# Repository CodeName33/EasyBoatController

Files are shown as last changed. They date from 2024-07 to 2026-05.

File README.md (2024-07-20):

# About

This is simple boat/yacht autopilot application (outboard motor only, not for sails). It uses android phone as main device and special diy hardware to move boat rudder.

# How to build hardware device

You need to buy some parts and print plastic parts with 3D Printer.

What to buy:
 - ESP32 Wroom

 - Nema 17 Stepper motor (17HS4401) (With cable)
 - Driver A4988

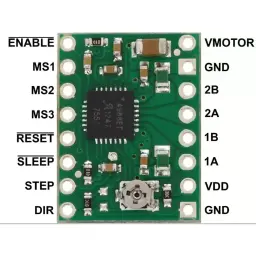
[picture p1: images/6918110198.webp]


 - Extension board for A4988

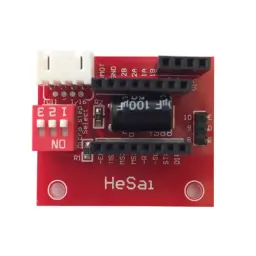
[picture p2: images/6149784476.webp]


 - Flange support bearing KFL08 8mm (2pc)

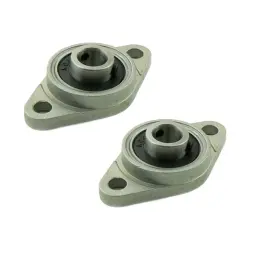
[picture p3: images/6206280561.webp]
 
 
 - Linear bearing LM8UU (2pc)
 - Round guide 8mm 500mm (2pc)

 - Rigid coupling 5x8

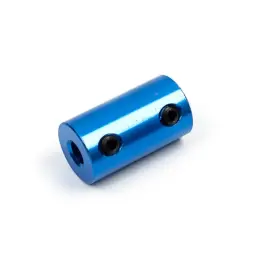
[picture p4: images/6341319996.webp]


 - Nut for screw TR8 pitch 2mm, stroke 8mm

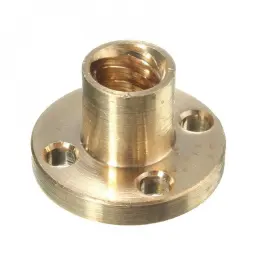
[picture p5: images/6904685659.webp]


 - Trapezoidal screw TR8x8 500mm

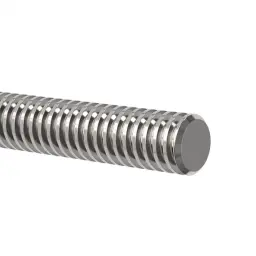
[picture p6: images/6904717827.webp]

 - 12v to 5v buck module (Any)
 - 12v accumulator
 - Bolts M3x10mm-12mm (4pcs), M3x16mm (4pcs)
 - Bolts M4x15mm (12pcs)
 - Bolts M5x30mm (2pcs), M5x25mm (1pc), M5x50mm (6pcs), M5x10mm (2pcs), M5x60mm (1pc)
 - Nuts M4 (12pcs)
 - Nuts M5 (12pcs)

Print all parts from Hardware/all-parts file. There are OpenSCAD source too, so you can change any parameters.

Hardware/how-to-assemble.3mf shows how to build. Black parts must be printed using hard plastic (I've used PETG carbon fibre) white parts can be printed using TPU.

Install A4988 to Extension board. Connect Nema 17 to Extension board.

Soldering:

E (Extension board) = GPIO4 (ESP32)

D (Extension board) = GPIO16 (ESP32)

S (Extension board) = GPIO17 (ESP32)

GND (Extension board, any GND) = GND (ESP32)

5v (Extension board) = 3v3 (ESP32)

9v (Extension board) = 12v+ (Power input)

12v+ (Power input) = IN+ (12v to 5v buck module)

12v- (Power input) = IN- (12v to 5v buck module)

OUT+ (12v to 5v buck module) = 5v (ESP32)

OUT- (12v to 5v buck module) = GND (ESP32)

Assembled device:
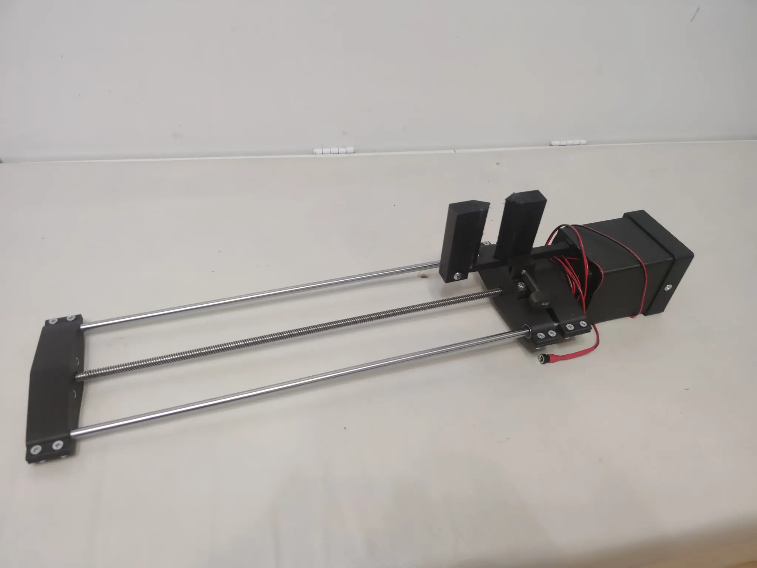
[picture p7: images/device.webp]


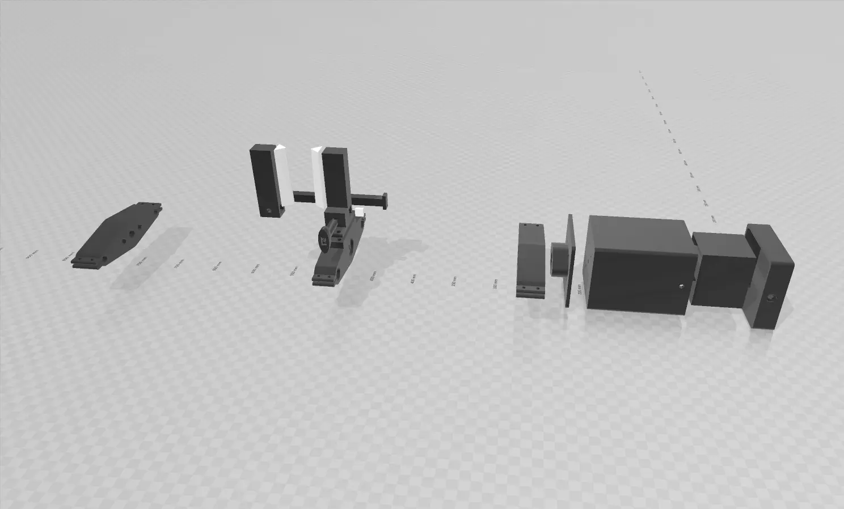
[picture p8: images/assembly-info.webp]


Use 2 fusion nut in holes at bottom of device (yes there are bottom and holes at bottom side). I've used 1/4 nut like in cameras and can use magic arms to hold device on boat.

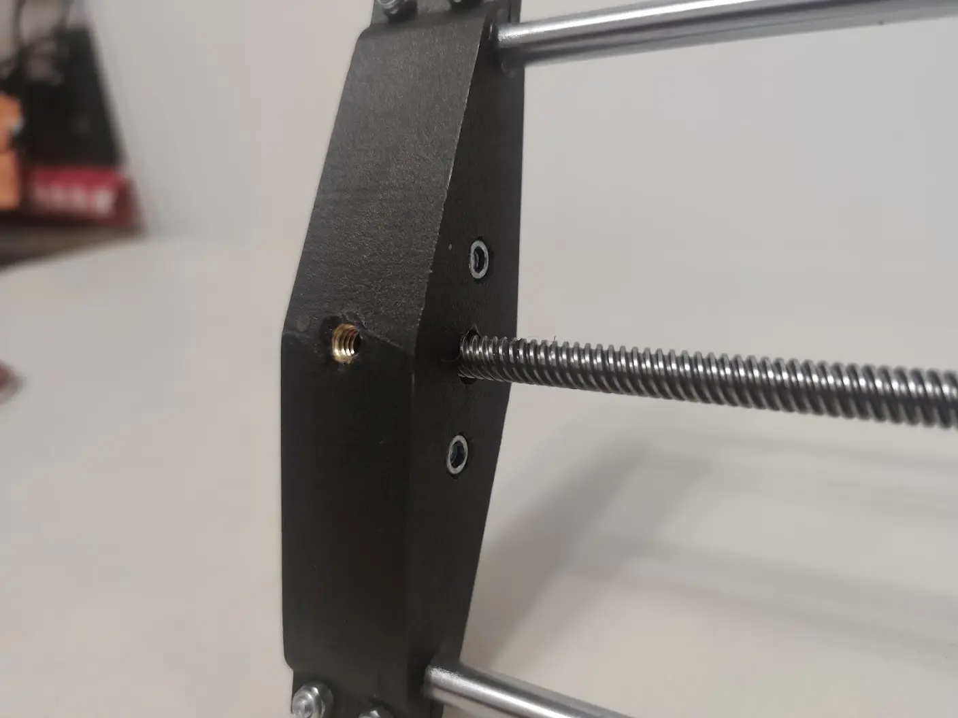
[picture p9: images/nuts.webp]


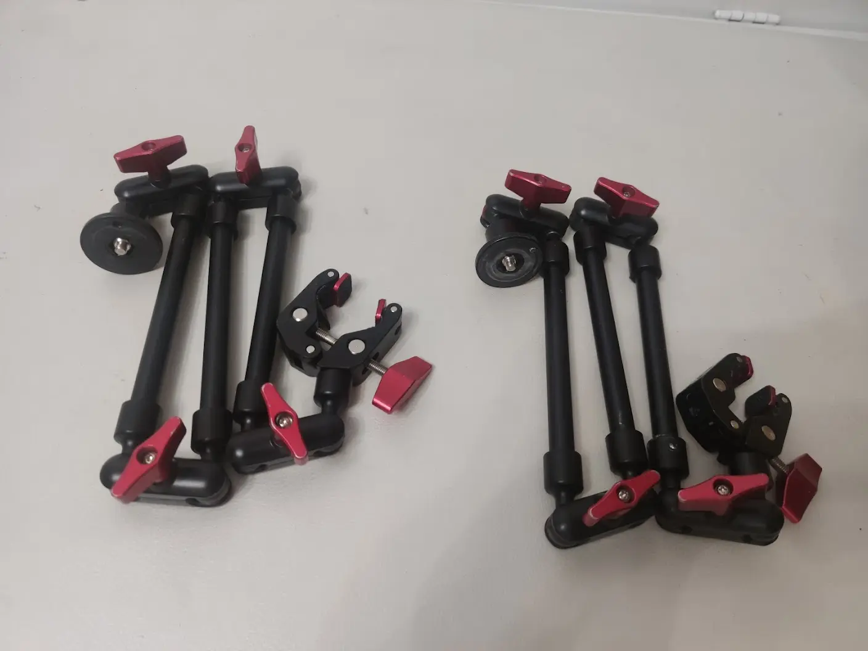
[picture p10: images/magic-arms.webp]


# Using Software

There are two ways:

1. Your own hosting for web-app (put manifest.json, index.htm and icon.png to your host)
2. Use my web-site (http://codename33.ru/apps/ebc/)

Using chrome on your mobile device on notebook goto http://codename33.ru/apps/ebc/ (or your own url).

Install EasyBoatController as desktop application. Now you have app installed (it will work even without internet after first run).

# Using Both parts

Power on hardware part (it has no buttons and indicators, just need to supply 12v power)

Press "Connect Bluetooth" button in EasyBoatController application. If all soldered right and worked you can see device named "EasyBoatController", connect to it.

Press "Calibrate" button and press "Run auto zero calibration" button. This will move caret to end and after some time to middle. 

Set the steering tiller level to zero and put tiller steering into tiller steering lock and lock it.

Now you can hold hardware device on boat. If you are using magic arms - fix device in current position.

You can test device using "Start Accel Drive" button. It will move the rudder when you when you tilt your phone (like in phone games).

For now this allication can't show maps but it can import route in KML or GPX format. You can make your own route in Navionics Boating or  this service for example (https://www.gpsvisualizer.com/draw/) and export GPX file.

In EasyBoatController application press "Route Management..." and next press "Import..." and open your GPX or KML file. You can save/load this route in application now.

Now you can start your engine wit preferred speed and press button "Start Navigation". 

**IMPORTANT NOTE**: You can't turn your screen off or switch to another application while navigating, web-apps can't work in background on android (Yes, ServiceWorkers, but no BLE for them). May be you want to rewrite my js code and make apk that can work in background, I don't want it now ;) I made special button called "Black Screen" it fills screen in black with some gray text on it. This can save battery for devices with OLED displays.

# Application Settings Description

**Course** - settings for navigation
 - **Maximum Rudder Position Percent** - zone in which rudder can move (100% - full)
 - **Keep Boat Near Lines** - In navigation mode this chack will force autopilot to move boat near lines between course points
 - **Taking Points Not Necessary** - If checked this means that boat don't need to move near points, to got it. It unchecked "Points - Distance To Point To Be Done" option works
 - **Keep Boat Near Line Q** - This value makes alutopilot try to move boat to line faster. Too high value can make boat make zigzags over line. 1.5 - 3.0 recommended.
 - **Keep Boat Near Line Max Percent** - very similar to "Keep Boat Near Line Q" option but in percents

 - **Points** - points options
     - **Distance To Point To Be Done** - works only when "Taking Points Not Necessary" unckecked. Distance in meters.

 - **Speed Compensation For Slow Rudder** - this algorythm use boat speed to limit rudder move zone (like "Maximum Rudder Position Percent" option). On high speed boat with slow rudder move speed it can help to navigate better.
     - **Enabled** - turns on or off this algorythm
     - **Compensate After Speed Kmh** - compensation will start after this speed (in km/h).
     - **Compensate Min Q** - minimum rudder zone (0.1 = 10% etc)
     - **Angle To Point Dont Compensate After** - Turn off compensation when difference between boat angle and cource angle more then this value,
**Gps** - GPS  options
 - **Use Compass Between Gps Steps** - it can increase cource accuracy, but you don't need to move youyr phone while navigating.
 - **Meters To Move** - GPS position must be changed to value more then in this option to calculate boat course. This option can help avoid course jumping cause of gps random inaccuracy (removed by default (0) in last version)
 - **Points To Group** - Algorythm takes averages GPS coordinates from count of this points. Also can help avoid course jumping cause of gps random inaccuracy
 
**Calibrate** - calibration options
 - **Max Steps** - max steps (from left to right position). If you use 500mm trapezoidal screw and round guides leave default
 - **Auto Calibration Center** - steps from side to center. If you use 500mm trapezoidal screw and round guides leave default
 - **Default Side Max** - default values for side to center that will be set after "Run auto zero calibration" button
 - **Inverted Move** - inversion for rudder

**Emulation** - emulation options
 - **Enabled** - turn on/off emulation mode
 - **Wind** - Wind in emulation
     - **Angle** - wind angle
     - **Force** - wind force. 0 - off, value - wind speed, but not in km/h in GPS distances (something like 0.00001)
 - **Offsets**
     - **Rudder Rotate** - static boat rotation (0 - off)
 - **Boat** - Boat options
     - **Speed** - boat speed,but not in km/h in GPS distances (something like 0.00002)
     - **Rudder Speed** - speed of rudder movements
     - **Delay Seconds** - delay for coordinates (GPS emulation) in seconds

**AccelDrive** - Accelerometer Drive Options
 - **Min Angle To Move** - minimum angle changes to accept. This can avoid many garbage changes.
 
# Some Videos

## EasyBoatController - Steering Wheel Test
IMAGE ALT TEXT (http://www.youtube.com/watch?v=HxvT-cGLmB0 "EasyBoatController - Steering Wheel Test")

## EasyBoatController - Rudder Lock Testing
IMAGE ALT TEXT (http://www.youtube.com/watch?v=xiY143fznu8 "EasyBoatController - Rudder Lock Testing")

## EasyBoatController - Movements Test
IMAGE ALT TEXT (http://www.youtube.com/watch?v=BEtO-wEw2SI "EasyBoatController - Movements Test")

## EasyBoatController - Short Creating And Testing
IMAGE ALT TEXT (http://www.youtube.com/watch?v=R22tecXQIwo "EasyBoatController - Short Creating And Testing")

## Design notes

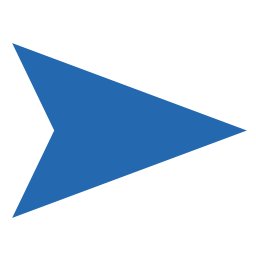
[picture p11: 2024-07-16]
Software/Web/boat.png

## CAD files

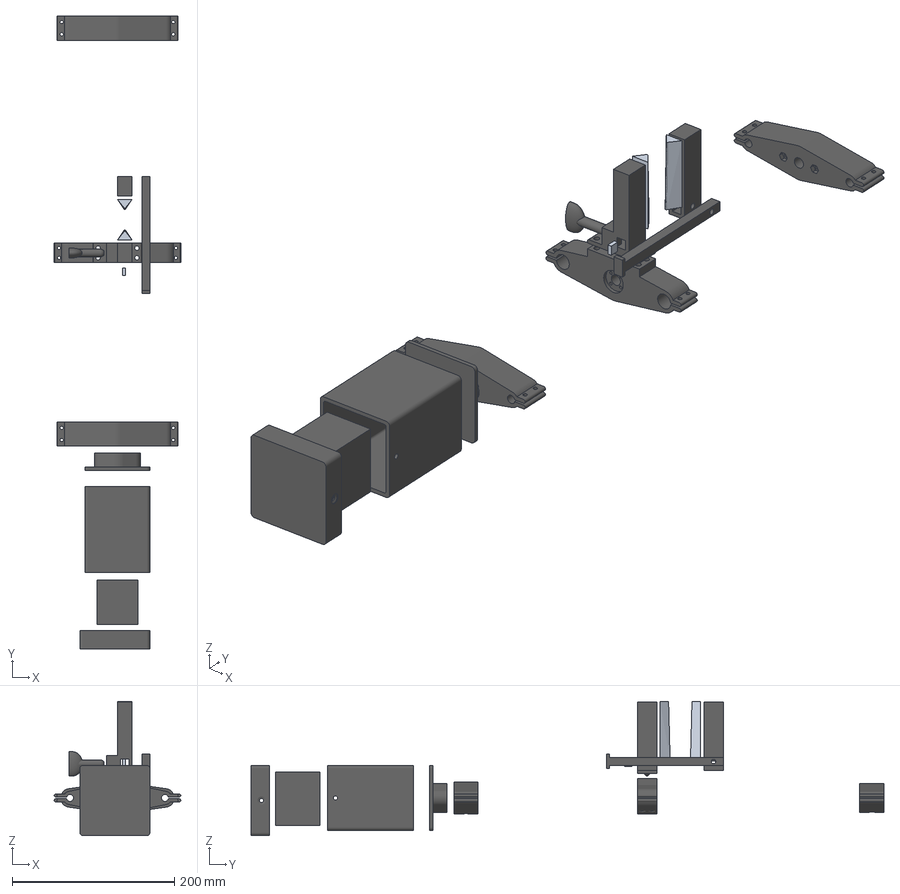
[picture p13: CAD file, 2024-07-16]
Hardware/how-to-assemble.3mf
156.0 x 780.0 x 165.5 mm

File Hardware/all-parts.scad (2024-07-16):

HolesExt = 0.5;
LayerHeight = 0.1666;

ShaftDiameter = 8 + HolesExt;
ShaftLength = 600;

ShaftHolderFullDiameter = 27 + HolesExt;
ShaftHolderWallsDiameter = 26 + HolesExt; 
ShaftHolderSideDiameter = 12 + HolesExt;
ShaftHolderHeightMin = 4.5;
ShaftHolderHeightMax = 8.5;
ShaftHolderRingDiameter = 13 + HolesExt;
ShaftHolderRingHeightMax = 12;
ShaftHolderBoltDiameter = 5 + HolesExt;
ShaftHolderBoltOffset = 18;
ShaftHolderNutHoleDiameter = 9.2;
ShaftHolderNutHeight = 4.5;

TubeDiameter = 8 + HolesExt;
TubeLength = 600;

ShaftTubeSpace = 50;
ShaftTubeSpaceCentered = ShaftTubeSpace + TubeDiameter / 2 + ShaftDiameter / 2;

BackHeight = 30;
TubeHoldersThick = 4;
TubeHoldersClampSpace = 2;
TubeHoldersClampLength = 8;
TubeHoldersClampBoltDiameter = 4;
TubeHoldersClampBoltsCount = 2;

MovingPartHeight = 14;
MovingPartMinHeight = 3.5;
MovingPartMinDiameter = 10 + HolesExt;
MovingPartMaxDiameter = 22 + HolesExt;
MovingPartBoltsSpace = 16;
MovingPartBoltDiameter = 3;

FrontHeight = 30;
FrontAdvancedDiameter = 4;

MotorSize = 42;
MoterBoltsSpace = 31;
MoterBigRoundDiameter = 22 + HolesExt;
MoterBigRoundHeight = 2.5;
MotorAddLength = 8.5;
MotorLength = 40;
MotorPlugWidth = 16;
MotorPlugHeight = 10;
MotorBoltDiameter = 3;
MotorRotateDiameter = 5;
MotorRound = 4;
MotorBoxSize = MotorSize + 30;
MotorBoxCapThick = 3;
MotorBoxCapWallsHeight = 20;
MotorBoxCapBoltDiameter = 5;
MotorBoxCapBoltCapDiameter = 10; //Fix!!!
MotorBoxCapGasketThick = 0.5;

ClutchDiameter = 16; //Fix
ClutchLength = 25; // Fix
ClutchAddLength = 13; //Fix

BearDiameter = 15;
BearLength = 24;

NutDiameter = 7.2;
NutLength = 8;
NutRoundSize = 18;
NutRoundOffset = 2;
NutRoundTop = 1.8;

ESP32Length = 52;
ESP32Width = 29;
ESP32Height = 6;

MotorPlateWidth = 35;
MotorPlateLength = 42;
MotorPlateHeight = 22;
MotorPlatePlugWidth = 13;

MotorBoxAdvSpace = 10;

AdapterHeight = ClutchAddLength + MotorAddLength;

MiddleHeight = BearLength;
MiddlePlaceWidth = 60;
MiddlePlaceHeight = 10;
MiddlePlaceBoltsOffset = 6;
MiddlePlaceBoltDiameter = 5 + HolesExt;
MiddlePlaceNutDiameter = 9.2;
MiddlePlaceNutHeight = 4.5;

SlidingProfileSize = 10;
HelmHolderHeight = 70;
SlidingProfileHolderLength = 5;
SlidingProfileHolderSize = SlidingProfileSize;
SlidingProfileHolderNutLength = 4.5; //FIX!!!
SlidingProfileHolderNutSize = 8.2; //FIX!!!
SlidingProfileHolderBoltDiameter = 5 + HolesExt;

SlidingProfileLength = 140;

fn = 512;
over = 0.01;
DetailsSpace = 90;

PartsCount = 10;

RenderSingle = "";

BoardsCaseThick = 1.5;
BoardsCaseLength = 55;
BoardsCaseSections = [30, 15, 15];
BoardsCaseWidth = 50;

function asum(array, length) = [ for (a=0, b=array[0]; a < length + 1; a= a+1, b=b+(array[a]==undef?0:array[a])) b ];


//Boards case
if (len(RenderSingle) == 0 || len(search("d", RenderSingle)) > 0)
translate([DetailsSpace * 3, DetailsSpace * (PartsCount - 10), 0]) {
	rotate([90, 0, 0])
	for (i = [0 : len(BoardsCaseSections) - 1]) {
		Heights = asum(BoardsCaseSections, i);
		Height = Heights[len(Heights) - 1];
		
		Base = Height - BoardsCaseSections[i] + BoardsCaseThick * i;
		BaseHeight = BoardsCaseSections[i] + BoardsCaseThick;
		translate([0, 0, Base]) {
			difference() {
				cube([BoardsCaseWidth, BoardsCaseLength, BaseHeight + BoardsCaseThick]);
				translate([BoardsCaseThick, -over, BoardsCaseThick]) cube([BoardsCaseWidth - BoardsCaseThick * 2, BoardsCaseLength + over *2 , BaseHeight - BoardsCaseThick]);
			}
		}
		
	}
}

//Bolt Fixer RotateCase
if (len(RenderSingle) == 0 || len(search("c", RenderSingle)) > 0)
translate([-DetailsSpace * 2, DetailsSpace * (PartsCount - 10), 0]) {
	BoltCaseHeight = 44;
	BoltDiameter = 5.4;
	BoltCaseThick = 2;
	BoltCaseCapSizeMax = 30;
	BoltCaseCapSizeMin = 12;
	BoltCaseCapHeight = 17;
	BoltCapHeight = 3;
	BoltCapDiameter = 9.5;
	BoltCaseTiameter = BoltDiameter + BoltCaseThick * 2;
	
	difference() {
		union() {
			resize([BoltCaseCapSizeMax, BoltCaseCapSizeMin, BoltCaseCapHeight]) {
				cylinder(h = BoltCaseCapHeight - BoltCaseCapSizeMin, d = BoltCaseCapSizeMax, $fn = 1024);
				translate([0, 0, BoltCaseCapHeight - BoltCaseCapSizeMin]) difference() {
					sphere(d = BoltCaseCapSizeMax, $fn = 512);
					rotate([180, 0, 0]) cylinder(h = BoltCaseCapSizeMax / 2, d = BoltCaseCapSizeMax, $fn = 1024);
				}
			}
			translate([0, 0, 0]) cylinder(h = BoltCaseHeight - BoltCaseTiameter / 2, d = BoltCaseTiameter, $fn = 1024);
			translate([0, 0, BoltCaseHeight - BoltCaseTiameter / 2]) sphere(d = BoltCaseTiameter, $fn = 512);
		}
		translate([0, 0, -0.01]) cylinder(h = BoltCaseHeight + 0.2, d = BoltDiameter, $fn = 1024);
		cube([BoltCapDiameter, BoltDiameter, BoltCapHeight * 2], center = true);
		cube([BoltDiameter, BoltDiameter, BoltCapHeight * 2 + LayerHeight * 4], center = true);
	}
}

//Slider Holder
if (len(RenderSingle) == 0 || len(search("b", RenderSingle)) > 0)
translate([-DetailsSpace, DetailsSpace * (PartsCount - 10), 0]) {
	cube([SlidingProfileHolderSize - HolesExt, SlidingProfileHolderSize - HolesExt, SlidingProfileHolderLength - 1 + over]);
}

//MotorBoxCap
if (len(RenderSingle) == 0 || len(search("a", RenderSingle)) > 0)
translate([0, DetailsSpace * (PartsCount - 10), 0]) {
	difference() {
		cuberounded([MotorBoxSize + TubeHoldersThick * 2 + MotorBoxCapThick * 2 + HolesExt, MotorBoxSize + TubeHoldersThick * 2 + MotorBoxCapThick * 2 + HolesExt, MotorBoxCapThick + MotorBoxCapWallsHeight], [1,2,3,4], radius = MotorRound, fn = fn);
		translate([MotorBoxCapThick + HolesExt / 2, MotorBoxCapThick + HolesExt / 2, MotorBoxCapThick - MotorBoxCapGasketThick]) cuberounded([MotorBoxSize + TubeHoldersThick * 2 + HolesExt, MotorBoxSize + TubeHoldersThick * 2 + HolesExt, MotorBoxCapWallsHeight + MotorBoxCapGasketThick + over], [1,2,3,4], radius = MotorRound, fn = fn);
		
		translate([(MotorBoxSize + TubeHoldersThick * 2 + MotorBoxCapThick * 2 + HolesExt) / 2, (MotorBoxSize + TubeHoldersThick * 2 + MotorBoxCapThick * 2 + HolesExt) / 2, MotorBoxCapThick + MotorBoxCapWallsHeight / 2]) 
		for (i = [0, 1]) {
			mirror([0, i, 0])
			translate([0, -(MotorBoxSize + TubeHoldersThick * 2 + MotorBoxCapThick * 2 + HolesExt) / 2 - over, 0])
				rotate([-90,0,0]) {
					cylinder(h = MotorBoxCapThick * 2, d = MotorBoxCapBoltDiameter, $fn = 128);
					cylinder(h = 1, d = MotorBoxCapBoltCapDiameter, $fn = 128);
					translate([0, 0, 1 - over]) cylinder(h = 1, d1 = MotorBoxCapBoltCapDiameter, d2 = MotorBoxCapBoltDiameter, $fn = 128);
			}
		}
	}
	//gasket
	translate([MotorBoxSize * 2, 0, 0]) cuberounded([MotorBoxSize + TubeHoldersThick * 2, MotorBoxSize + TubeHoldersThick * 2, MotorBoxCapGasketThick], [1,2,3,4], radius = MotorRound, fn = fn);
}

//Sliding Profile
if (len(RenderSingle) == 0 || len(search("9", RenderSingle)) > 0)
translate([0, DetailsSpace * (PartsCount - 9), 0]) {
	translate([0, SlidingProfileSize * 2, 0]) rotate([90, 0, 0]) difference() {
		union() {
			cube([SlidingProfileLength, SlidingProfileSize - HolesExt / 2, SlidingProfileSize - HolesExt / 2]);
			translate([SlidingProfileLength, 0, -TubeHoldersThick]) cube([TubeHoldersThick, SlidingProfileSize - HolesExt / 2, SlidingProfileSize - HolesExt / 2 + TubeHoldersThick * 2]);
		}
		translate([ MiddleHeight / 2, - over,  SlidingProfileHolderSize / 2 + HolesExt / 4]) {
			rotate([-90, 0, 0])
			cylinder(h = SlidingProfileHolderSize + over * 2, d = SlidingProfileHolderBoltDiameter, $fn = 128);
		}
	}
}

//Rubber Part
if (len(RenderSingle) == 0 || len(search("8", RenderSingle)) > 0)
translate([0, DetailsSpace * (PartsCount - 8), 0]) {
	for (i = [ 0, 1 ]) {
		mirror([i, 0, 0])
		{
			translate([10, -HelmHolderHeight / 2, 0]) {
				hull() {
					cube([SlidingProfileSize + TubeHoldersThick * 2, HelmHolderHeight, 0.01]);
					translate([SlidingProfileSize /2 + TubeHoldersThick, 0, 10]) rotate([-88.5, 0, 0]) scale ([1,0.6,1]) difference() { 
						cylinder(h = HelmHolderHeight, d =  TubeHoldersThick / 2, $fn = fn);
						translate([-(SlidingProfileSize + TubeHoldersThick * 2) / 2, 0, -over]) cube([SlidingProfileSize + TubeHoldersThick * 2,SlidingProfileSize + TubeHoldersThick * 2,HelmHolderHeight + over * 2]);
					}
				}
			}
		}
	}
}

//Middle Top Sliding Part
if (len(RenderSingle) == 0 || len(search("7", RenderSingle)) > 0)
translate([0, DetailsSpace * (PartsCount - 7), 0]) {

	difference() {
		union() {
			translate([0, -MiddleHeight / 2, TubeHoldersThick]) {
				difference() {
					cube([SlidingProfileSize + TubeHoldersThick* 2,  MiddleHeight, SlidingProfileSize + TubeHoldersThick* 2]);
					translate([TubeHoldersThick, -over, TubeHoldersThick]) cube([SlidingProfileSize,  MiddleHeight + over * 2, SlidingProfileSize]);
				}
			}
			translate([0, -MiddleHeight / 2, TubeHoldersThick * 2 + SlidingProfileSize]) {
				cube([SlidingProfileSize + TubeHoldersThick* 2,  MiddleHeight, HelmHolderHeight]);
			}

		}
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

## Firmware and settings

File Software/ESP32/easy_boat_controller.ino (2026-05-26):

#include <BLEDevice.h>
#include <BLEServer.h>
#include <BLEUtils.h>
#include <BLE2902.h>


BLEServer* pServer = NULL;
BLECharacteristic* pStatusCharacteristic = NULL;
BLECharacteristic* pControlCharacteristic = NULL;
bool deviceConnected = false;
bool oldDeviceConnected = false;
uint32_t value = 0;
long currentStep = 0;
long targetStep = 0;
long statusCurrentStep = currentStep;
long statusTargetStep = targetStep;
//FastAccelStepperEngine engine = FastAccelStepperEngine();
//FastAccelStepper *stepper = NULL;

namespace drivers {
  const int A4988 = 0;
  const int TMC2209 = 1;
}

namespace settings {
  const int driver = drivers::TMC2209;
  const long statusDelay = 200;
  const long pingDelay = 1000;
  namespace pins {
    const int enable = 4;
    const int dir = 16;
    const int step = 17;
  }
}

namespace calibration {
  long minValue = 0;
  long maxValue = 0;
  long zeroValue = 0;
}

const int ledPin = 2; // Use the appropriate GPIO pin for your setup

#define SERVICE_UUID        "82c2e3b5-6b5f-4437-8941-bade7c66cbf6"
#define STATUS_CHARACTERISTIC_UUID "91a184db-3822-4136-aeac-305727992cfe"
#define CONTROL_CHARACTERISTIC_UUID "47431b0f-1164-4027-8efa-38c44b51de88"


class CMotorController
{
  private:
    int pinE;
    int pinD;
    int pinS;
    long pos = 0;
    long target = 0;
    long steps = 256;
    long csteps = 0;
    long workStep = 0;
    int operationStep = 0;
    unsigned long stepWait = 64;
    unsigned long releaseWait = 64;
    unsigned long stepTimer = 0;
    bool enabled = false;
  public:
    CMotorController(int pinE_, int pinD_, int pinS_, int driver = drivers::TMC2209) : pinE(pinE_), pinD(pinD_), pinS(pinS_) {

      if (driver == drivers::A4988) {
        steps = 50;
        stepWait = 700;
        releaseWait = 700;
      } else if (driver == drivers::TMC2209)  {
        steps = 256;
        stepWait = 64;
        releaseWait = 64;
      }

      pinMode(pinE, OUTPUT);
      digitalWrite(pinE, HIGH); //OFF

      pinMode(pinD, OUTPUT);
      digitalWrite(pinD, LOW);

      pinMode(pinS, OUTPUT);
      digitalWrite(pinS, LOW);
    }

    void setEnabled(bool value) {
      if (!inProgress() || value) {
        digitalWrite(pinE, value ? LOW : HIGH);
        enabled = value;
      }
    }

    bool inProgress() {
      return (pos != target);
    }

    long getPos() {
      return pos;
    }

    long getTarget() {
      return target;
    }

    void setTarget(long value) {
      target = value;
    }

    void setZero() {
      pos = 0;
      target = 0;
      operationStep = 0;
      workStep = 0;

    }

    void onTime() {
      if (pos != target) {
        if (workStep == 0) {
          if (!enabled) {
            setEnabled(true);
          }
          Serial.print("enabled: ");
          Serial.println(enabled);
          workStep = (pos < target ? 1 : -1);
          
        }
      }

      if (workStep != 0) {
        if (operationStep == 0) {
          digitalWrite(pinD, workStep > 0 ? LOW : HIGH); //Direction
          digitalWrite(pinS, HIGH);
          stepTimer = micros();
          operationStep = 1;
        }

        if (operationStep == 1) {
          if (micros() - stepTimer > stepWait) {
            digitalWrite(pinS, LOW);
            stepTimer = micros();
            operationStep = 2;
          }
        }

        if (operationStep == 2) {
          if (micros() - stepTimer > releaseWait) {
            operationStep = 0;
            csteps++;
            if (csteps >= steps) {
              csteps = 0;
              pos = pos + workStep;
              workStep = 0;
            }
          }
        }
      }
    }
};
CMotorController motorController(settings::pins::enable, settings::pins::dir, settings::pins::step, settings::driver);

class MyServerCallbacks: public BLEServerCallbacks {
  void onConnect(BLEServer* pServer) {
    deviceConnected = true;
  };

  void onDisconnect(BLEServer* pServer) {
    deviceConnected = false;
  }
};

long parseLong(const char *value, long defaultValue = 0) {
  if (value == nullptr) {
    return defaultValue;
  }
  long multiplier = 1;
  if (*value == '-') {
    multiplier = -1;
    value++;
  }
  long v = 0;
  while (*value >= '0' && *value <= '9') {
    v = v * 10 + (*value - '0');
    value++;
  }
  return v * multiplier;
}

void readParams(const char *commandline) {
  while (*commandline != 0) {
    const char *command = commandline;
    while (*commandline != ':') {
      if (*commandline == 0) {
        return;
      }
      commandline++;
    }
    long commandLength = commandline - command;
    commandline++;
    const char *value = commandline;
    while (*commandline != ',' && *commandline != 0) {
      commandline++;
    }

    long valueLength = commandline - value;

    if (commandLength == 1) {
      if (*command == 'T') {
        targetStep = parseLong(value);
        motorController.setTarget(targetStep);
      } else if (*command == 'Z') {
        motorController.setZero();
      } else if (*command == 'E') {
        long evalue = parseLong(value);
        motorController.setEnabled(evalue != 0);
      } else if (*command == 'C') {
        long evalue = parseLong(value);
        currentStep = evalue;
      }
      
    }

    if (*commandline != ',') {
      *commandline++;
    }
  }
}

bool onWriteBusy = false;
unsigned long onWriteTimer = 0;
class MyCharacteristicCallbacks : public BLECharacteristicCallbacks {
  void onWrite(BLECharacteristic* pControlCharacteristic) {
    String value = pControlCharacteristic->getValue();
    if (value.length() > 0) {
      Serial.print("control: ");
      Serial.println(value); // Print the integer value
      readParams(value.c_str());

      onWriteBusy = true;
      onWriteTimer = millis();
      
      //delay(300);
      
    }
  }
};

bool bluetoothBusy = false;
unsigned int bluetoothTimer = 0;

void setup() {
  Serial.begin(115200);
  pinMode(ledPin, OUTPUT);
  

  /*
  digitalWrite(settings::pins::enable, LOW);


  for (int i = 0; i < 10000; i++) {
    digitalWrite(settings::pins::step, HIGH);
    delayMicroseconds(200);
    digitalWrite(settings::pins::step, LOW);
    delayMicroseconds(1000);
  }
  */

  //digitalWrite(settings::pins::enable, HIGH);

//settings::pins::enable, settings::pins::dir, settings::pins::step
/*
  engine.init();
  stepper = engine.stepperConnectToPin(settings::pins::step);
  if (stepper) {
    stepper->setDirectionPin(settings::pins::dir);
    stepper->setEnablePin(settings::pins::enable);
    stepper->setAutoEnable(true);

    stepper->setSpeedInHz(500);       // 500 steps/s
    stepper->setAcceleration(100);    // 100 steps/s²
    stepper->move(1000);
  }*/

  //motorController.setEnabled(true);

  BLEDevice::init("EasyBoatController");

  pServer = BLEDevice::createServer();
  pServer->setCallbacks(new MyServerCallbacks());

  BLEService *pService = pServer->createService(SERVICE_UUID);
  pStatusCharacteristic = pService->createCharacteristic(STATUS_CHARACTERISTIC_UUID, BLECharacteristic::PROPERTY_READ | BLECharacteristic::PROPERTY_WRITE | BLECharacteristic::PROPERTY_NOTIFY | BLECharacteristic::PROPERTY_INDICATE);
  pControlCharacteristic = pService->createCharacteristic(CONTROL_CHARACTERISTIC_UUID, BLECharacteristic::PROPERTY_WRITE);
  pControlCharacteristic->setCallbacks(new MyCharacteristicCallbacks());

  pStatusCharacteristic->addDescriptor(new BLE2902());
  pControlCharacteristic->addDescriptor(new BLE2902());

  pService->start();

  BLEAdvertising *pAdvertising = BLEDevice::getAdvertising();
  pAdvertising->addServiceUUID(SERVICE_UUID);
  pAdvertising->setScanResponse(false);
  pAdvertising->setMinPreferred(0x0);
  BLEDevice::startAdvertising();
  Serial.println("Waiting a client connection to notify...");
}

unsigned long emulationTimer = 0;
void emulation() {
  if (millis() - emulationTimer > 10) {
    if (currentStep != targetStep) {
      if (currentStep > targetStep) {
        currentStep--;
      } else if (currentStep < targetStep) {
        currentStep++;
      }
    }
    emulationTimer = millis();
  }
}

unsigned long statusDelayTimer = 0;
void loop() {
  if (onWriteBusy) {
    if (millis() - onWriteTimer > 300) {
      onWriteBusy = false;
    }
  }
  //curren tStep = 
  if (deviceConnected) {
    if (millis() - statusDelayTimer > settings::statusDelay) {
      if (motorController.getPos() != statusCurrentStep || motorController.getTarget() != statusTargetStep || millis() - statusDelayTimer > settings::pingDelay) {
        statusCurrentStep = motorController.getPos();
        statusTargetStep = motorController.getTarget();
        String status =  String("C:") + String(statusCurrentStep) + String(",T:") + String(statusTargetStep);
        pStatusCharacteristic->setValue(status.c_str());
        pStatusCharacteristic->notify();
        Serial.print("status: ");
        Serial.println(status);
        statusDelayTimer = millis();
      }
      //delay(300); // bluetooth stack will go into congestion, if too many packets are sent, in 6 hours test i was able to go as low as 3ms
    }
  }
  //emulation();
  // disconnecting
  if (!deviceConnected && oldDeviceConnected && !bluetoothBusy) {
    Serial.println("Device disconnected.");
    bluetoothBusy = true;
    bluetoothTimer = millis();
    //delay(500); // give the bluetooth stack the chance to get things ready
    
  }

  if (bluetoothBusy) {
    if (millis() - bluetoothTimer > 500) {
      pServer->startAdvertising(); // restart advertising
      Serial.println("Start advertising");
      oldDeviceConnected = deviceConnected;
      bluetoothBusy = false;
    }
  }
  // connecting
  if (deviceConnected && !oldDeviceConnected && !bluetoothBusy) {
    // do stuff here on connecting
    oldDeviceConnected = deviceConnected;
    Serial.println("Device Connected");
  }
  motorController.onTime();
}
